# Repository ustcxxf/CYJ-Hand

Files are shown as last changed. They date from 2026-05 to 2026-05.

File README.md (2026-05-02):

# Customize-Your-Joy-hand (CYJ-Hand)

&emsp;&emsp;Humanoid dexterous hands have significant potential in pros-thetics, service robotics, and high-performance manipulation. However, existing designs often struggle to balance the chal-lenging requirements of lightweight design, high biomimicry, personalized customization, and low cost. To address these challenges, we present the CYJ Hand (Customize-Your-Joy Hand), an innovative 22-DOF humanoid dexterous hand. Fea-turing a highly biomimetic structure, the CYJ system weighs only 750 grams（forearm included）. Its modular design supports user-oriented customization while simplifying assembly, maintenance, and functional expansion. Inspired by Da Vinci’s mechanics, the CYJ Hand integrates a novel, controllable ten-don mechanism that allows for reconfigurable tendon routing and actuation system to meet diverse needs. Constructed with 3D printing and affordable commercial materials, the hardware cost for the CYJ Hand structure (excluding actuators) is under $60. Experimental results demonstrate that the CYJ Hand achieves a 100% success rate in both the Kapandji Test and GRASP taxonomy, and further exhibits dynamic grasping, in-hand manipulation, sub-millimeter motion repeatability (~0.7 mm), and reliable load-bearing performance, validating its exceptional dexterity and biomimetic design. With its com-prehensive advantages and innovations， the CYJ Hand pro-vides a versatile platform for the future applications and re-search in personalized prosthetics and dexterous robotic ma-nipulation, bridging the gap between high dexterity and acces-sibility in humanoid robotics. Related files and methods are open-sourced at GitHub repository.

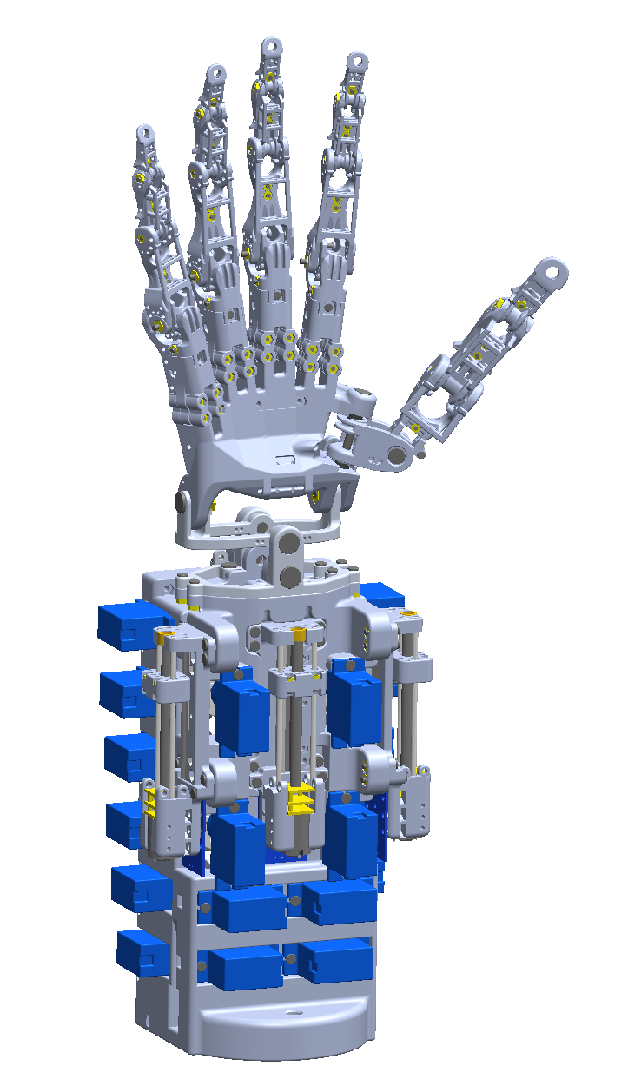
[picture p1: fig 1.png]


<center><font size=3><b>Figure 1 </b> CYJ Hand + Arm</font></center>

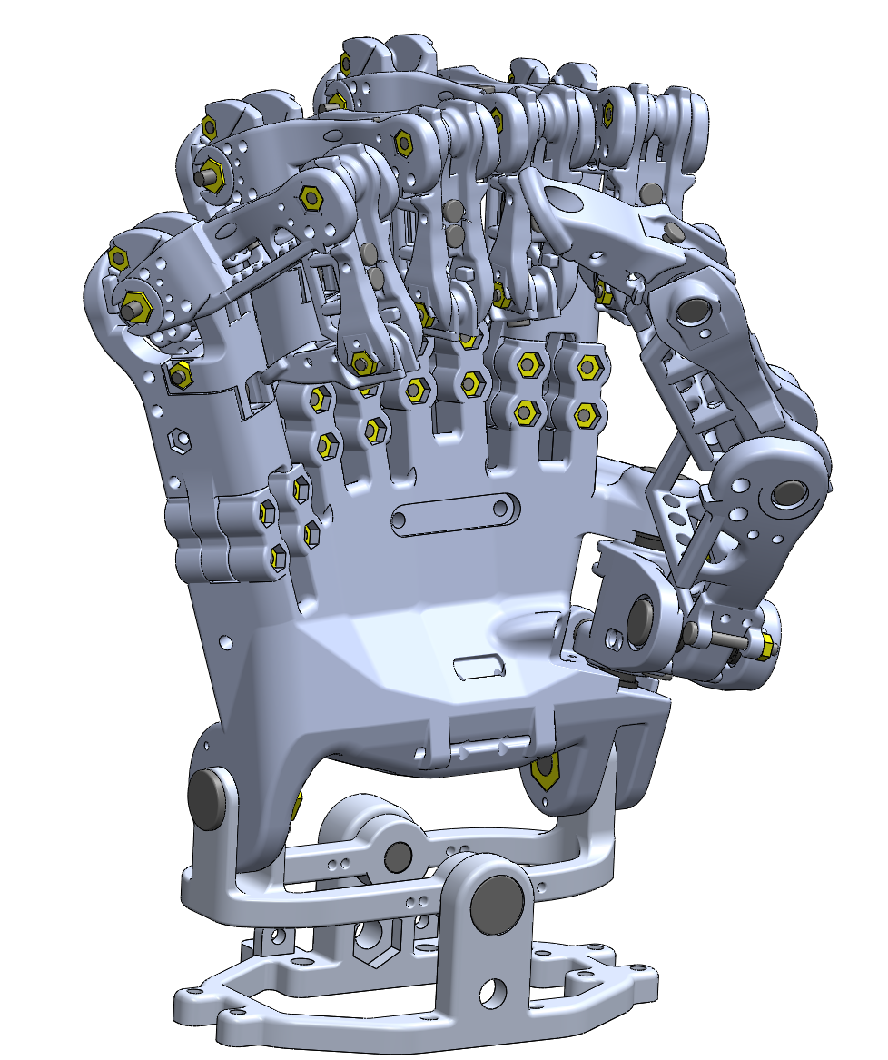
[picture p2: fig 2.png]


<center><font size=3><b>Figure 2 </b> CYJ Hand</font></center>

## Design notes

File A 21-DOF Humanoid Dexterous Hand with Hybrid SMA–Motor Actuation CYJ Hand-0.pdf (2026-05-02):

1

Abstract—CYJ Hand-0 is a 21-DOF humanoid dexterous hand featuring a hybrid tendon-driven actuation system that combines shape memory alloys (SMAs) and DC motors. The hand employs high-strength fishing line as artificial tendons and uses a fully 3D-printed AlSi10Mg metal frame designed to replicate the skeletal and tendon-muscle structure of the human hand. A linear motor-driven module controls finger flexion, while an SMA-based module enables finger extension and lateral abduction. These modules are integrated into a compact hybrid actuation unit mounted on a custom rear support structure. Mechanical and kinematic experiments, conducted under an Arduino Mega 2560-based control system, validate the effectiveness of the design and demonstrate its biomimetic dexterity.
Index Terms-- Humanoid dexterous hand, hybrid actuation, tendon-driven mechanism, 3D printing, biomimetic robotics
I. INTRODUCTION
From the late 20th century to the early 21st century, the concept of “robots” has transitioned from science fiction into tangible reality. Initially designed for simple, specialized tasks, robots have progressively undertaken increasingly complex, precise, and critical roles in industry and military. Among these, robotic manipulators stand as the earliest industrial robots and the foundation of modern robotics, liberating humans from laborious tasks and facilitating mechanization and automation. Moreover, they operate effectively in hazardous environments, thereby enhancing safety in sectors including machinery manufacturing, metallurgy, electronics, light industry, and nuclear energy.
The human hand represents the pinnacle of biological evolution, exhibiting extraordinary dexterity and versatility. Humanoid dexterous hands (HDHs) strive to replicate the intricate form, structure, and function of the human hand to enable similarly flexible and delicate manipulation. They hold immense promise for diverse applications spanning medical assistance, domestic services, intelligent manufacturing, space exploration, oceanic development, and public safety [1].
The history of prosthetic hands dates back to Roman times circa 200 B.C., where early wooden prostheses primarily served cosmetic or rudimentary functional purposes. The 19th century witnessed the invention of the tendon-driven, single-degree-of-freedom prosthetic hand by Peter Baliff, powered by the user’s limb movement—a fundamental principle that persists in contemporary prosthetics. The advent of the Belgrade hand [2] by Tomovic and Bonic in 1962

*Research supported by the National Science Foundation of China (Grant number: 61773358).
All authors are associated with the key Laboratory of Precision and Intelligent Chemistry, Institute of Humanoid Robots, Department of Precision Machinery and Precision Instrumentation, University of Science and Technology of China, Hefei, Anhui, 230026, PRC (*Corresponding author is Erbao Dong and can be contacted at e-mail: ebdong@ustc.edu.cn) marked a milestone, ushering in a new era of HDHs research. Since then, academic institutions and technology companies worldwide have pursued extensive research, yielding significant advancements such as the Okada hand [3], Stanford/JPL hand [4], Utah/MIT hand [5], and Robonaut hand [6]. With the advent of the 21st century, breakthroughs in sensor technology, human-computer interaction, bionics, and artificial intelligence have driven the evolution of HDHs towards greater diversity, miniaturization, and intelligence, exemplified by innovations like the Cyber hand[7], Tokyo hand [7] and UT hand [8].
Despite these advances, existing HDHs are often constrained by limited structural biomimicry, insufficient degrees of freedom (DOF), inadequate sensory capabilities, limited flexibility and coordination, low load-bearing capacity, fragile impact resistance, and high manufacturing costs. To address these challenges, the CYJ Hand-0 proposed herein incorporates the following key features:
- A highly biomimetic skeletal and joint structure with 21 DOFs (excluding the wrist).
- A flexible tendon-driven system utilizing high-strength fishing line.
- A hybrid actuation scheme integrating a shape memory alloy (SMA) linear drive module with double-amplified stroke and a DC brush motor linear drive module.
- Integration of the actuation system into a custom-designed robotic arm.
- Fabrication through cost-effective, easily manufacturable AlSi10Mg metal 3D printing, resulting in a total mass of only 380 grams.
- A fundamental control system based on the Arduino Mega2560 microcontroller for single-finger and full-hand operation.
- Single-finger load capacity of 1.2 kgf and an overall hand load capacity of 8 kgf.
- Capability to perform all Kapandji tests, 32 distinct gesture actions, and over 30 grasping experiments.
The remainder of this paper is structured as follows: The first section elaborates on the hand’s overall structural design, key components, kinematic modeling, and mechanical analysis of the flexible tendon drive. The second section details the SMA linear flexible drive module, DC brush motor linear drive module, system integration, and control framework. The last section presents performance evaluations in force, motion, dexterity, and grasping ability. Finally, the Conclusion summarizes the work and discusses future research directions.

II. MATERIALS AND METHODS
A. Bionic principle

## A 21-DOF Humanoid Dexterous Hand with Hybrid SMA-Motor Actuation: CYJ Hand-0 *

Jin Chai, Xiang Yao, Mengfan Hou, Yanghong Li and Erbao Dong*

2

The human hand’s main anatomical structures can be categorized into eight primary components: bones, tendons, ligaments, muscles, blood vessels, nerves, fatty tissue, and skin. The skeletal system is notably complex, comprising a total of 27 bones, which include 8 carpal bones, 5 metacarpal bones, and 14 phalanges [9]. The carpal bones are located within the wrist and are classified as radial or ulnar based on their anatomical position. The metacarpal bones articulate with the carpal bones at their bases via the carpometacarpal (CMC) joints, while the phalanges of each finger connect to the metacarpophalangeal (MCP) joints proximally. For the four fingers other than the thumb, each joint chain consists of the MCP joint, proximal interphalangeal (PIP) joint, and distal interphalangeal (DIP) joint, progressing from the proximal to the distal end. Due to mechanical constraints inherent to the interphalangeal joints, the MCP joint allows flexion and extension between 0° and 90°, and lateral deviation between –15° and 15°. The PIP joint exhibits a flexion range from 0° to 110°, while the DIP joint allows motion from 0° to 90° [10]. Furthermore, based on anatomical principles, the DIP joint flexes simultaneously with the PIP joint in the index, middle, ring, and little fingers, establishing a dynamic intra-finger coupling. This relationship is mathematically expressed in Eq.
(1) and illustrated in Fig. 1.
(1)

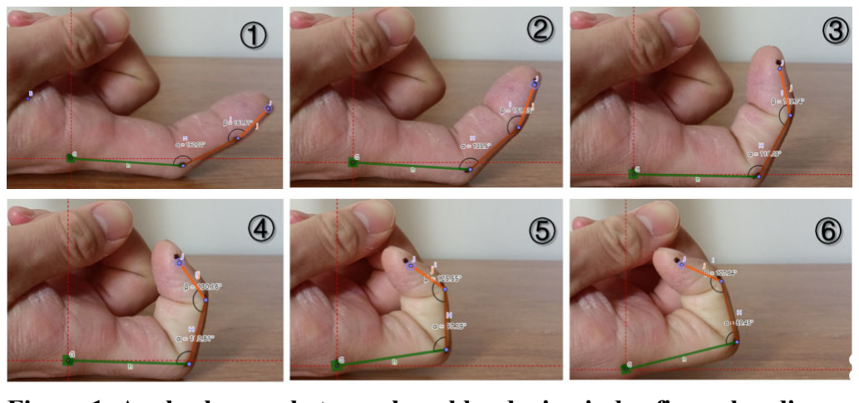
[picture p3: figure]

The structure of the thumb differs from that of the other four fingers in that it comprises only three joints: the carpometacarpal (CMC), metacarpophalangeal (MCP), and distal interphalangeal (DIP) joints, lacking a proximal interphalangeal joint. The thumb’s carpometacarpal joint, also known as the trapeziometacarpal (TMC) joint, grants it significantly greater mobility and strength compared to the other fingers. This joint facilitates a wide range of motions, including rotation (~17°), adduction and abduction (~42°), flexion and extension (~45°), as well as opposition—the ability to cross the palm. Consequently, the thumb exhibits exceptional dexterity. Traditionally, the TMC joint was considered to have 3-DOF [11], which, combined with the rest of the hand, results in a total of 21-DOF. However, subsequent research has revealed that the articular surfaces between the trapezium and the first metacarpal are saddle-shaped, with the axes for adduction-abduction (Ab-Ad) and flexion-extension (Fl-Ex) being neither orthogonal nor intersecting [12]. Most contemporary biomimetic hands, such as the Etho hand, implement the thumb’s TMC joint as a 2-DOF ball joint. While ball-and-socket joints provide smooth movement that approximates 2-DOF, their structural configuration differs from that of the human thumb and typically requires up to three actuators and six tendons for control.
The DOFs of the human hand are commonly simplified to

### 20 by omitting subtle motions, including active or passive

rotation of each finger around its longitudinal axis [13] (as illustrated in Fig. 2a), the complex kinematics of the thumb’s

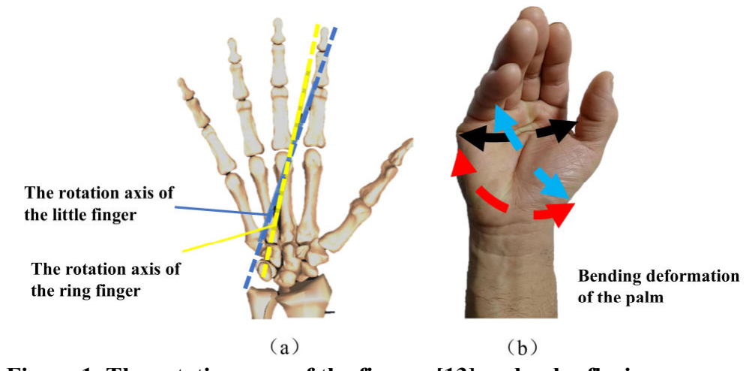
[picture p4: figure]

TMC joint, flexion and deformation of the palm (Fig. 2b), and the DOFs of the wrist.
B. Overall structure and 3D prototype
The overall structural design of the CYJ Hand-0 is illustrated in Fig. 3a. All components are named according to their anatomical counterparts in the human hand, including the thumb, index finger, middle finger, ring finger, little finger, metacarpals, carpals, and wrist. Notably, the thumb's metacarpal structure is divided into two distinct segments: the medial adduction carpometacarpal joint and the rotational carpometacarpal joint, which will be described in detail later. In addition, the index, middle, and ring fingers adopt a unified structural design to simplify fabrication and enhance component interchangeability.
As shown in Fig. 3b, the CYJ Hand-0 consists of 18 distinct component types, totaling 80 individual parts. To improve modularity and reduce manufacturing costs, many joints share identical components. The hand is not only anatomically inspired in appearance but also replicates the skeletal structure of a human hand at a 1:1 scale in both form and assembly, as depicted in Fig. 3c. The total mass of the hand is 380 g, which accounts for less than 0.575% of the body weight of an average 75 kg adult male (approximately 413 g for a human hand). As shown in Fig. 3d, the unique mechanical design of the bionic hand enables up to 21 DOFs, excluding the wrist.
C. Structural design of key components
The index finger structure of the CYJ Hand-0 serves as a universal design, also applied to the middle and ring fingers. Each universal finger consists of 9 distinct component types—including the proximal, middle, and distal phalanges—resulting in a total of 12 individual parts. To ensure optimal functional performance and structural integrity, the design incorporates sliding bearings and adopts a biomimetic shape that closely replicates the interphalangeal joints of the human finger. The structural layout and dimensions of the universal finger are shown in Fig. 4. The little finger differs from this universal structure only in the length of the proximal phalanx and a few minor structural details, as illustrated in Fig. 5a.

Figure 1. Angle changes between knuckles during index finger bending.

Figure 1. The rotation axes of the fingers [13] and palm flexion.

3

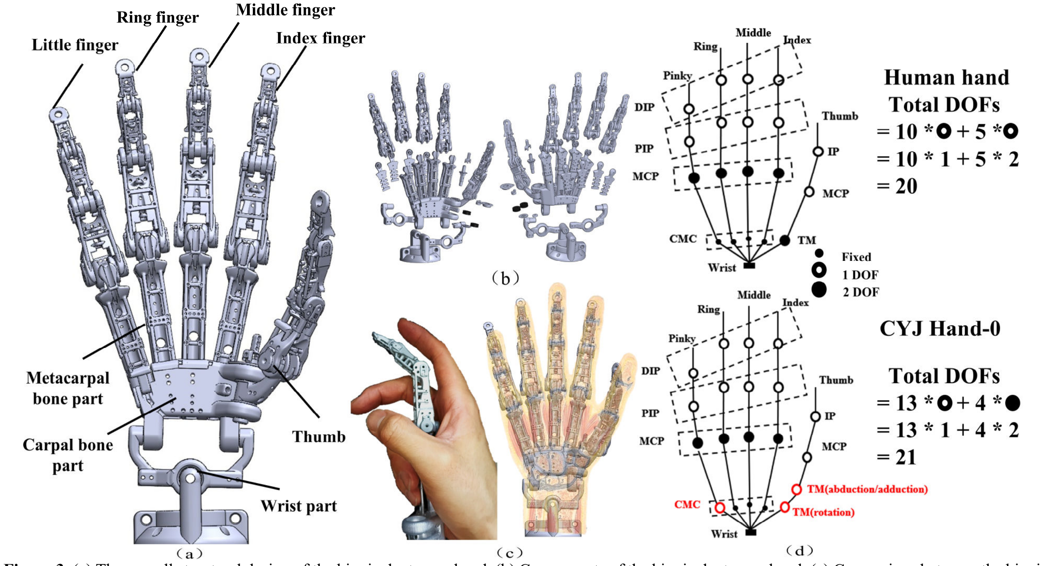
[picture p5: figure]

The thumb, being the most flexible and complex digit of the CYJ Hand-0, adopts a customized structural design. To balance structural simplicity with functional fidelity, the thumb’s metacarpal is divided into two segments at the carpometacarpal (CMC) joint: one responsible for adduction/abduction and the other for flexion/extension. The adduction/abduction module is structurally similar to the metacarpophalangeal (MCP) joints of the other fingers. This design choice reduces the overall degrees of freedom, enhances joint modularity, and simplifies mechanical implementation, as shown in Fig. 5b.
The joint rotation ranges of the CYJ Hand-0 are designed to match those of the human hand and are compared with representative existing bionic hands in Table I.
TABLE I. | COMPARISONS OF THE HDHS
Hand | Weight (g) | Interphalangeal joint rotation angle | Thumb joint rotation angle
MCP (°) | PIP (°) | DIP (°) | Ab-Ad (°) | Ex-Fl (°)
Human hand | 431 | 0-90 | 0-110 | 0-90 | 0-70 | 0-70
CYJ Hand-0 | 380 | 0-90 | 0-110 | 0-90 | 0-53 | 0-107
Robotic hand | | 0-90 | 0-110 | 0-90 | 0-90 | 0-90
Tact hand | 350 | 0-90 | 23-90 | 0-20 | 0-90 | 0-105
Dextrus hand | 428 | 0-90 | 0-90 | 0-90 | 0-90 | 0-120
Bebionic hand | 550 | 0-90 | 0-90 | 0-20 | | 0-68
i-Limb hand | 600 | 0-90 | 0-90 | 0-20 | 0-60 | 0-95
The metacarpal bones of the human hand are numerous, tightly packed, and arranged in a complex three-dimensional configuration. To enhance the anatomical fidelity of the palmar structure in the CYJ Hand-0—while minimizing unnecessary internal space and reducing weight—an interchangeable metacarpal design and an integrated carpal bone structure were developed, as illustrated in Fig. 5c. Notably, the metacarpal bones of the four fingers and the base connecting to the carpal region are not arranged in a parallel manner. Instead, they are positioned at specific angles relative to one another, forming a naturally concave geometry

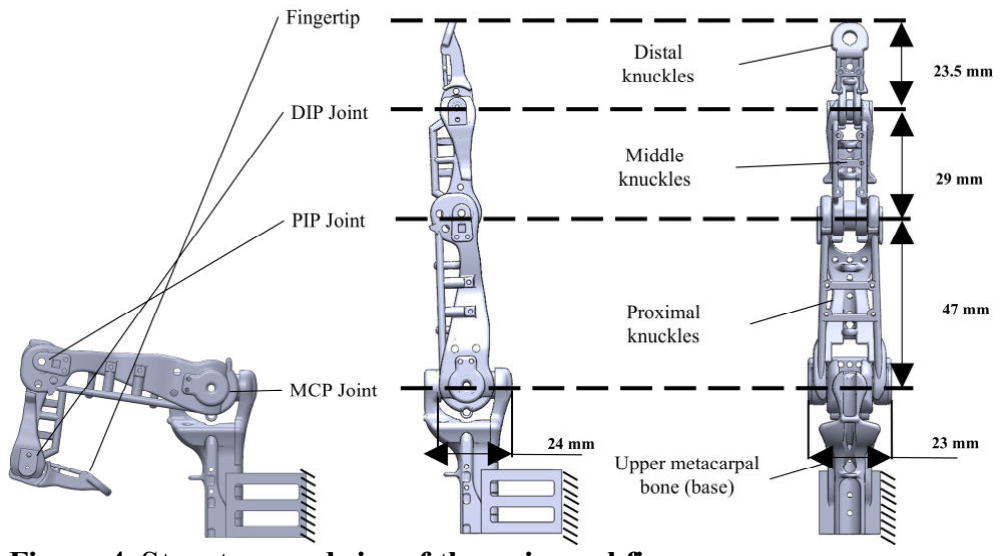
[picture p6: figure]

that mimics the human palm. This curvature enables the CYJ Hand-0 to achieve a cupped palm configuration, thereby enhancing its grasping performance, as shown in Fig. 5d.
D. Kinematic modeling of the fingers
Each finger of the CYJ Hand-0 can be thought of as a small, open-chain, rotationally articulated, tandem robot. The entire hand is equivalent to multiple such robots connected in parallel. The universal finger mechanism belongs to the side-swinging type 4-joint finger structure, as shown in Fig. 6a. The axes of joints 1 and 2 at the metacarpophalangeal joint are orthogonal to each other. Joints 3 and 4 represent the proximal and distal phalanges respectively. The axes of joints 2, 3 and 4 are always parallel. the finger linkage coordinate system is established according to the D-H theory, as shown in Fig. 6b.
Define | as the fixed reference coordinate system 0.
Define the origin as the point where the axes of joints 1 and 2 intersect. X and Y form the right-handed system. The lengths

Figure 3. (a) The overall structural design of the bionic dexterous hand. (b) Components of the bionic dexterous hand. (c) Comparison between the bionic dexterous hand and human hand. (d) Comparison of DOFs between the bionic dexterous hand and human hand.

Figure 4. Structure and size of the universal finger.

4

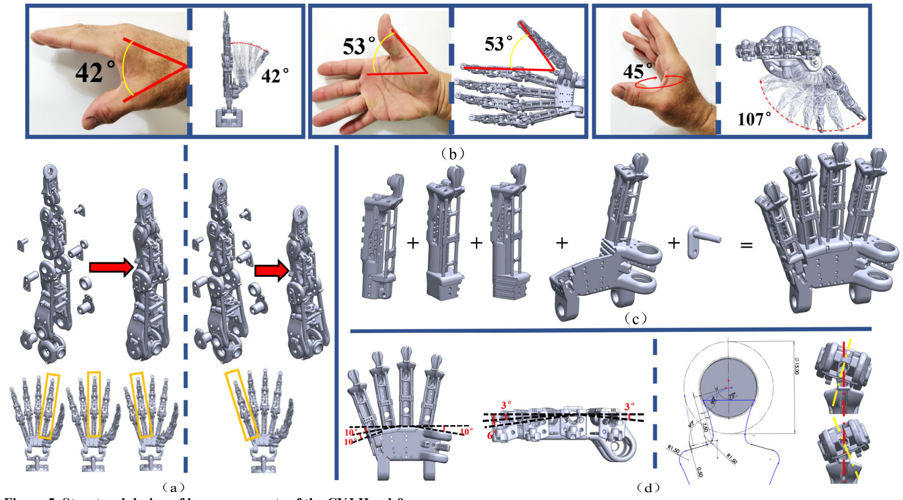
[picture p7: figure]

of the phalanges are , , and . The angles of rotation of
the joints are | , | , | and | . The axes of the lateral
pendulum joints at the metacarpophalangeal joints are perpendicular to the axes of the flexion joints at
angles | . The coordinates of the position of the finger
tip in the fixed reference system are | . See Table Ⅱ
below for detailed D-H parameters.

TABLE II. D-H PARAMETERS FOR THE UNIVERSAL FINGERS

1 0 | 0 | 0 | -15~15
2 90 | 47 | 0 | 0~90
3 0 | 29 | 0 | 0~110
4 0 | 23.5 | 0 | 0~90
The following paragraph discusses the solution to forward kinematics for a finger. The homogeneous transformation matrix that describes the position and orientation of the coordinate system at the fingertip relative to the fixed
Therefore, with known values of , | , | and | , the
position coordinates | of the general fingertip can be

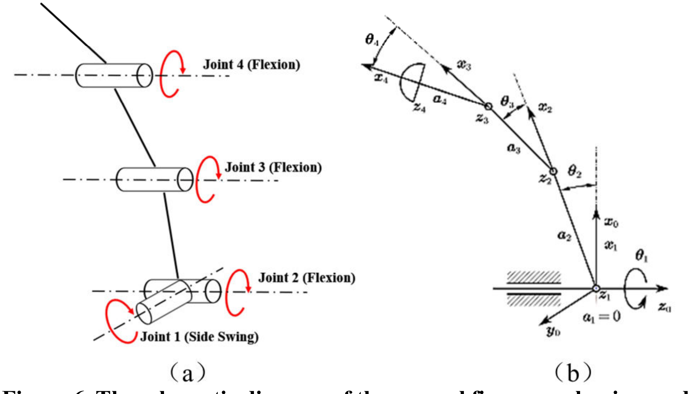
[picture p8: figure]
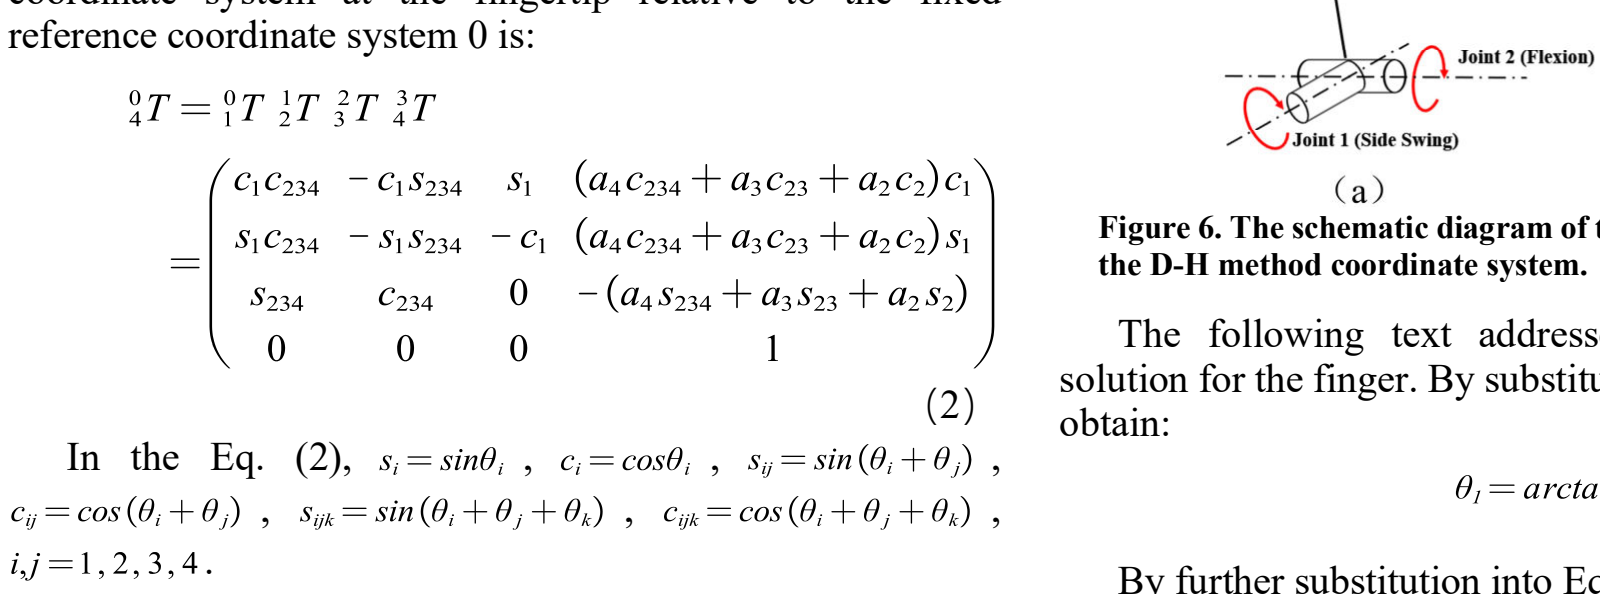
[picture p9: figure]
reference coordinate system 0 is:; In the Eq. (2),; obtain:; the D-H method coordinate system.

The following text addresses the inverse kinematics solution for the finger. By substituting into Eq. (3) and (4), we

(6)

By further substitution into Eq. (1), we obtain:
（7）

Figure 6. The schematic diagram of the general finger mechanism and

Figure 5. Structural design of key components of the CYJ Hand-0.

5

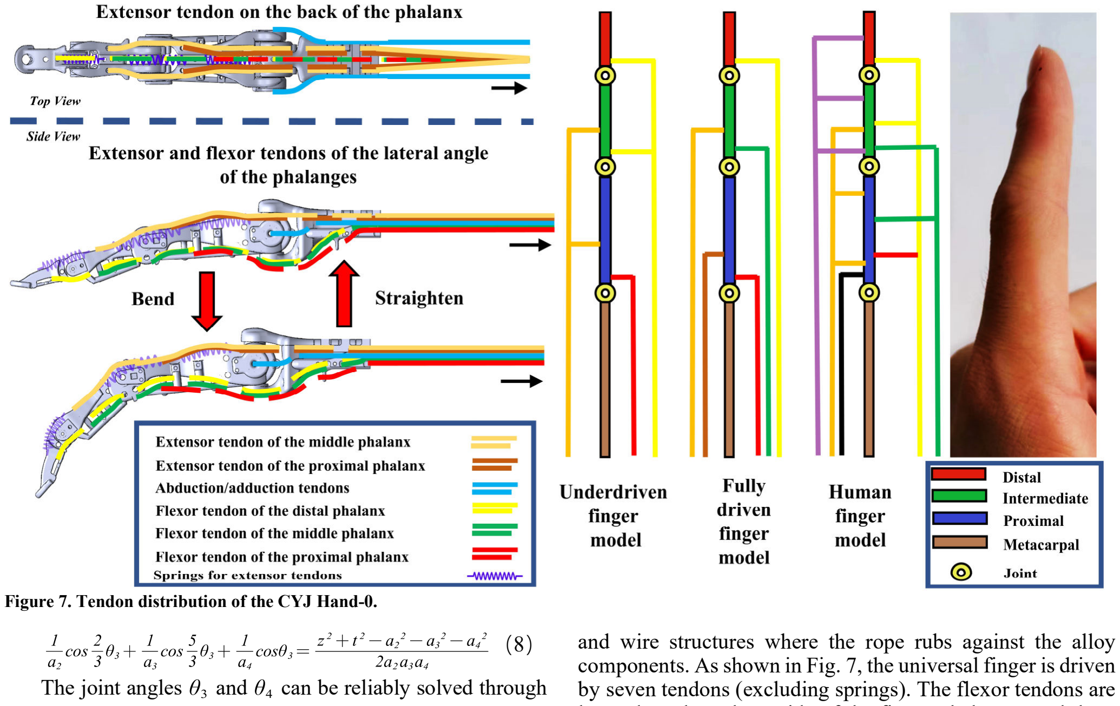
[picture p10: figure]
The joint angles; and; can be reliably solved through

numerical methods, and then substituted back into Eq. (3) to solve for using Newton's iteration method. Thus, with the known position coordinates of the fingertip ((x, y, z)), the joint
angles , , | and | can be determined.
E. Numerical simulation for finger tendon
The CYJ Hand-0 utilizes high-powered fishing line as a tendon. These tendons are fixed at one end to the phalanges and connected to linear actuators at the other, transmitting force and torque over a distance. Such tendons possess high strength, light weight, and an ability to absorb impacts that gear transmissions lack. Here we use a 12-braid high-powered fishing line with a mark of 9.0, a diameter of 0.55mm and a nominal maximum pull of 40kg. At the distal end of the tendons, the rope is commonly secured using the figure-eight loop method and the double fisherman's knot technique.

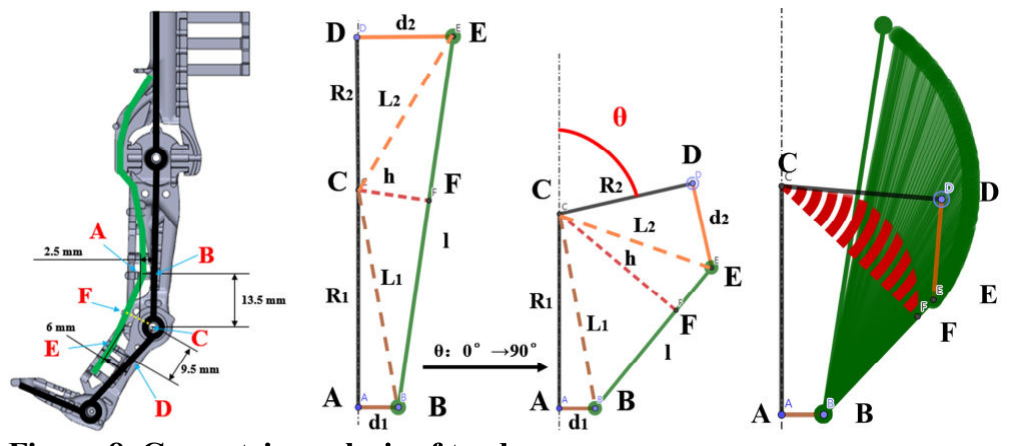
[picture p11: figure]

The tendons have a fixed path of travel at each finger joint. Grease is used to reduce friction at the edges of holes, tubes and wire structures where the rope rubs against the alloy components. As shown in Fig. 7, the universal finger is driven by seven tendons (excluding springs). The flexor tendons are located on the palmar side of the finger phalanges and there are three of them that drive the proximal, middle and distal phalanges in flexion. The extensor tendons, located on the dorsal side of the finger phalanges, are two in number and drive the proximal and middle phalanges to extend back to their original positions. The distal phalanx is not driven by an additional tendon and is reset by a pre-tensioned spring. The two abduction/adduction lateral tendons, located on both sides of the finger, with one side stretching while the other relaxes when the finger swings.
The metacarpophalangeal joint, proximal and distal knuckles have the same configuration. Among them, the proximal phalangeal joint has a high load-bearing capacity and is more frequently used in the human hand. We take it as the object of analysis in GeoGebra, and the analysis is shown

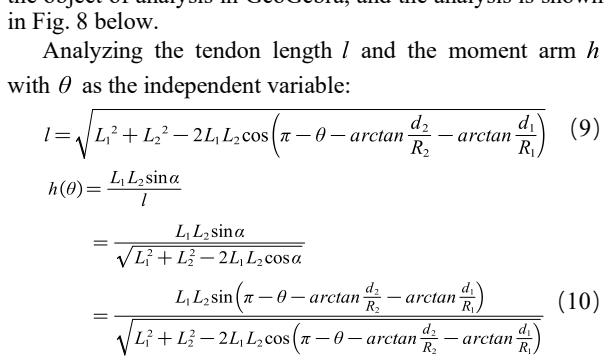
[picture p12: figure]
in Fig. 8 below.; with as the independent variable:

Analyzing the tendon length and the moment arm

Substitute the data of the proximal joint of the universal finger to plot and analyze. As shown in Fig. 9a, the red line represents the tendon length at the joint and the black line represents the fitted straight line. The tendon length gradually

Figure 7. Tendon distribution of the CYJ Hand-0.

Figure 8. Geometric analysis of tendons.

6

shortens by 16.86 mm over the course of the joint angle from 0° to 110°. It means that at least 20 mm of work needed to be done at the driver end of the straight line. This means that the linear actuator needs to perform work at least a 20mm distance. As shown in Fig. 9b, the red line represents the force arm of the tendon and the black line represents the fitted straight line, which increases over the course of the joint angle from 0° to 90°. The increase in the force arm reduces the stretching force on the tendon, making it easier for the finger to perform the

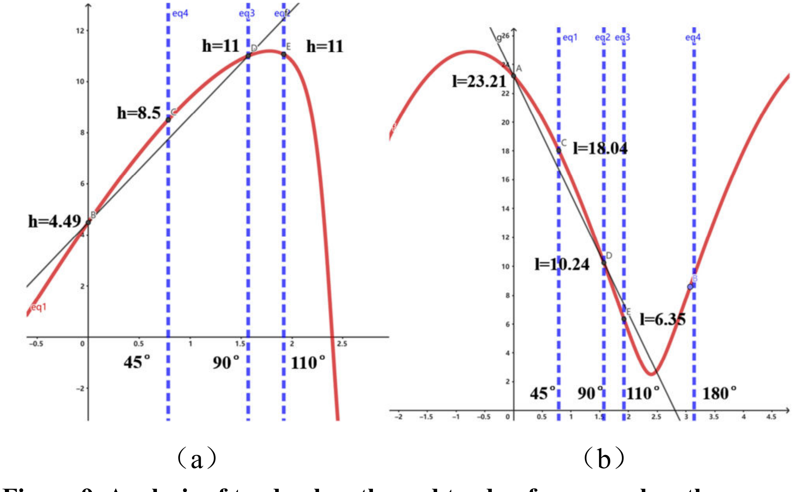
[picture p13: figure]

bending maneuver under load and to output a greater force/moment at the end of the finger.
III. DESIGN AND CONSTRUCTION OF THE DRIVE SYSTEM
The integrated solution of the driven system of the CYJ Hand-0 is an important innovation of the overall design. Unlike traditional motor or pneumatic/hydraulic drives, the bionic dexterity hand introduces not only a DC brush motor drive module system to drive the finger flexion, but also an SMA linear drive module system to drive the finger side-swing and straightening movements. They form the SMA-motor hybrid driven module system together.
A. Abbreviations and Acronyms
The SMA driven module uses Ni-Ti alloy wires of DYNALLOY from US (detailed parameters as shown in Table Ⅲ). The SMA material has a shape memory effect, which is a deformability and workability resulting from the martensite-austenite phase change that occurs between low and high temperatures of the material. The method of controlling the module is energized heating. The maximum displacement output is 18 mm and the maximum output force is 784 N. The module construction is shown in Fig. 10.

TABLE III. PARAMETERS OF SMA WIRE
Parameters | Value
Density | 6.45g/cm³
Phase transition temperature | 90°C
Specific heat capacity | 837J/(kg·K)
Thermal conductivity | 18W/(m·K)
Poisson's ratio | 0.33
Coefficient of martensitic thermal expansion | 6.6×10⁻⁶ /°C
Coefficient of austenitic thermal expansion | 11.0×10⁻⁶ /°C
B. Motor driven module
Finger flexion is driven by a screw nut motor (GA12-N20-298, parameters shown in Table IV) drive module. The module drives the tendons to rotate the phalanges relative to the joints so that the fingers are flexed. A single motor driven module has dimensions of 73.25mm in height, 33mm in length, and 25mm in width, with a working stroke of 20mm, a self-weight of 40g, and a rated output force of 400N. The models of the motor and the motor driven module are shown in Fig. 11.

TABLE IV. PARAMETERS OF SMA WIRE
Parameters | Value
Rated voltage | 12 V
Rated current | 0.18 A
Rated speed | 100 RPM

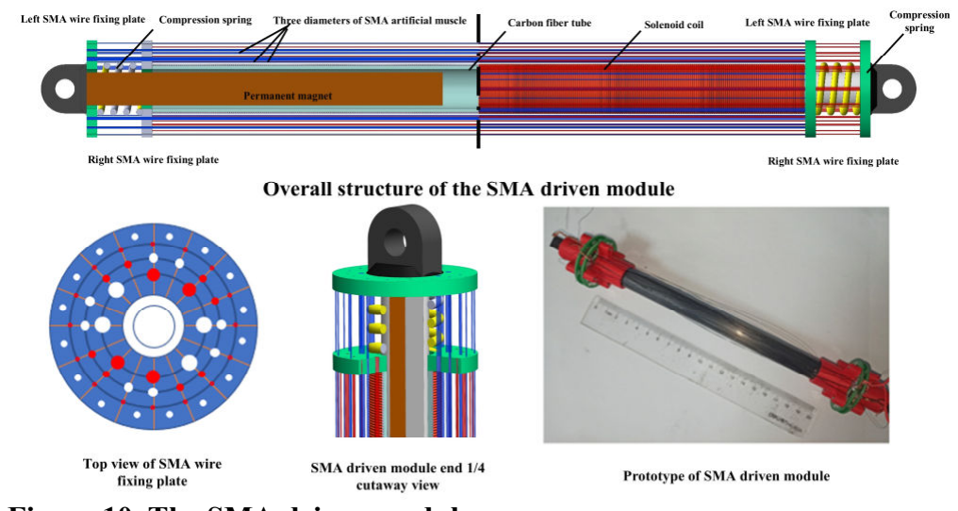
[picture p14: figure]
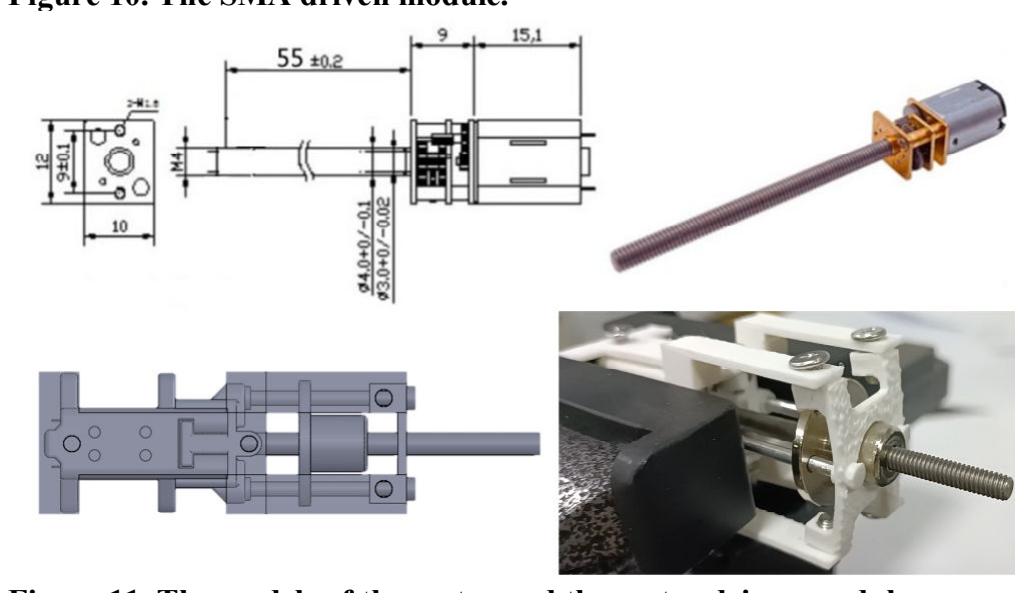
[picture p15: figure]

Rated torque | 1.5 kg·cm
Pitch of screw | 0.7 mm
C. The integrated SMA-motor hybrid driven system
In the SMA driven module, SMA wires of larger diameter have a lower response frequency and higher output force. SMA wires of smaller diameter have a higher response frequency and lower output force. Besides, the electromagnetic coil and permanent magnet in the SMA driven module can make up for the shortcomings of the SMA wires. They can form a linear driven module with adjustable size of output force, frequency and fast response speed. The
Figure 9. Analysis of tendon lengths and tendon force arm lengths. | Figure 10. The SMA driven module.

Figure 11. The models of the motor and the motor driven module

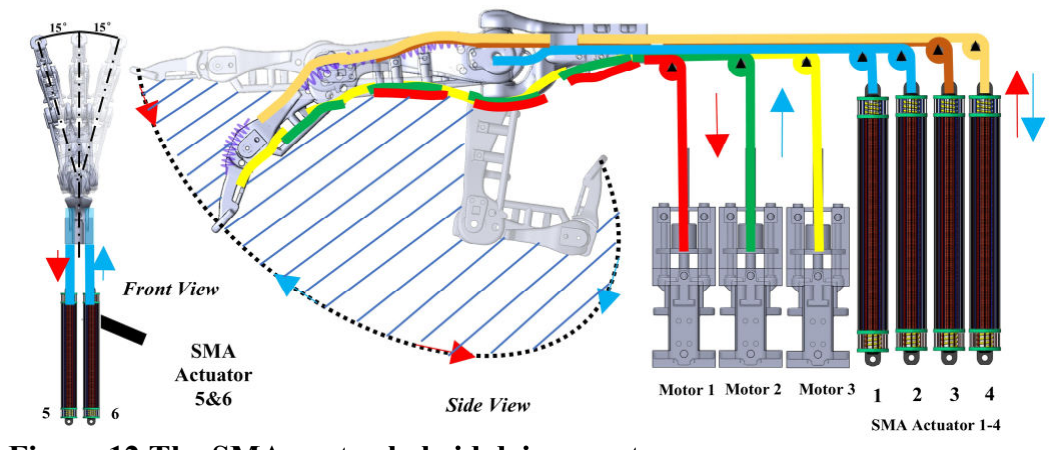
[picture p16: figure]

Figure 12 The SMA-motor hybrid driven system.

7

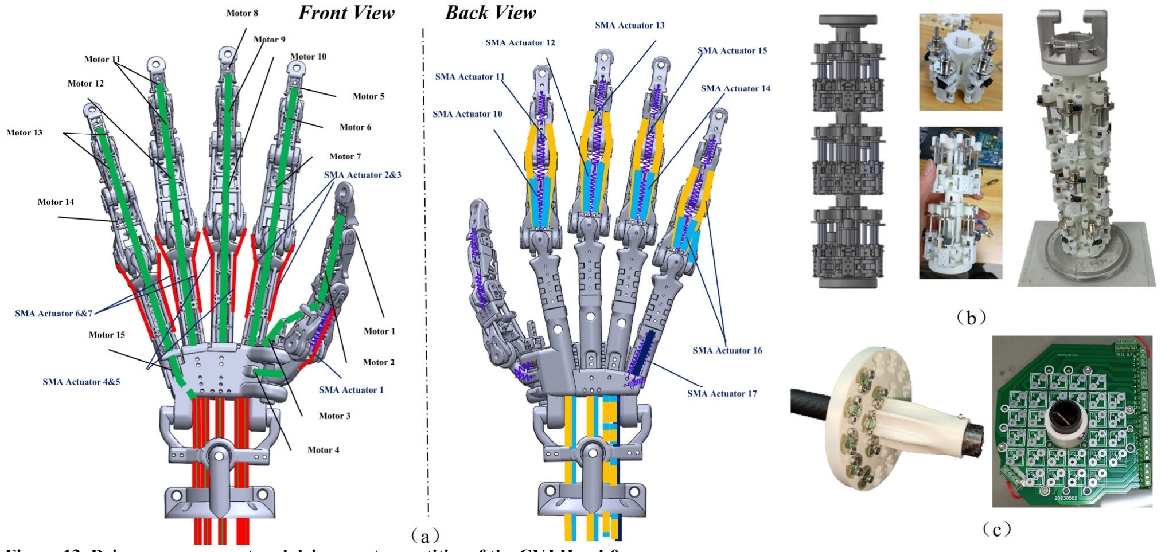
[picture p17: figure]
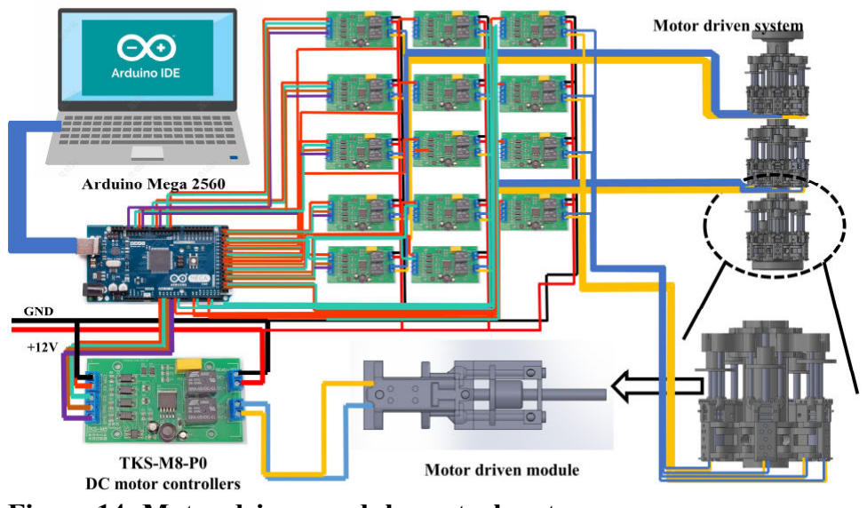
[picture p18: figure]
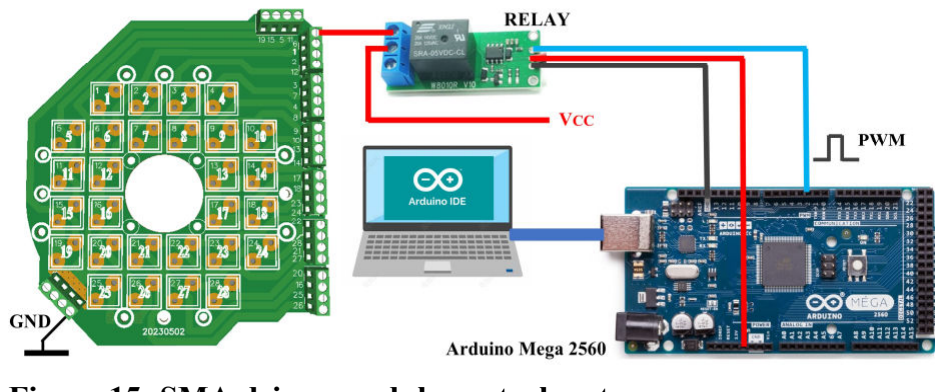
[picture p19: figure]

motor driven module features a small but stable output force, self-locking capability, high output displacement accuracy and slow speed (1.17mm/s). As a result, the hybrid driven system constructed by combining the two driven modules has the particularly comprehensive advantages of adjustable response frequency, high output force range and high output displacement accuracy.
As shown in Fig. 12, the motor driven module drives the finger flexion. With the help of the spring, the SMA linear actuator module drives the finger to straighten or to swing sideways. When the finger is flexed, the motor turns the screw forcibly, causing the nut to drop and the flexor tendon to be stretched. At this time, the SMA linear drive module maintains its original length and the extensor tendon relaxes. As the finger is straightened, the motor drives the screw to reverse the rotation of the nut, causing the flexor tendon to relax. At this point the SMA driven module is energized and heated and the extensor tendon is tensed. The SMA wires and the spring on the back of the phalanx together drive the phalanx to extend until it returns to its original position. After the finger is returned to its original position, the SMA driven module is switched off to dissipate heat and the extensor tendons are relaxed as the SMA wires are restored to their original length. The CYJ Hand-0 has a total of 21 DOFs. The total number of actuators (TNA) is 32, with a total of 17 SMA driven

Figure 13. Driven arrangement and driven system entities of the CYJ Hand-0.

Figure 14. Motor driven module control system.

Figure 15. SMA driven module control system.

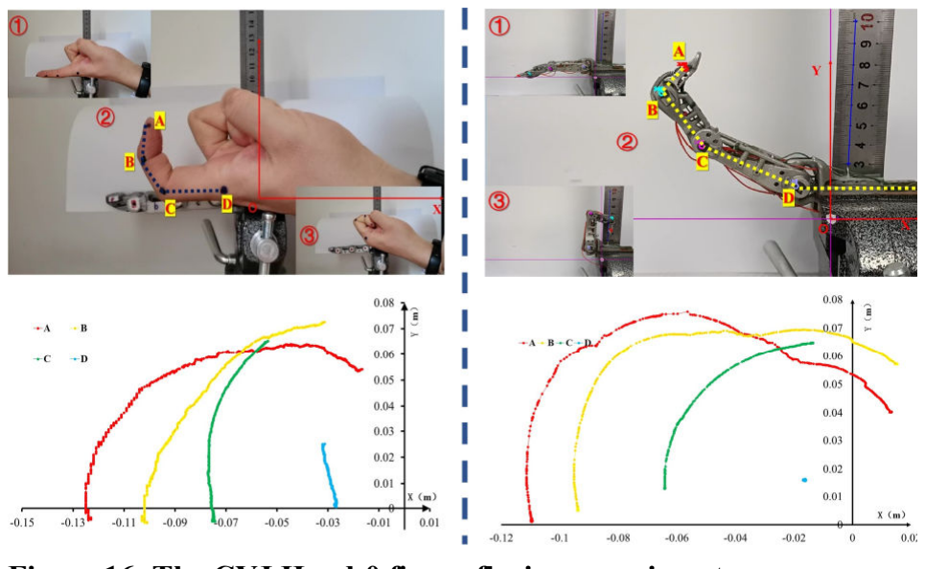
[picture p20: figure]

Figure 16. The CYJ Hand-0 finger flexion experiment.

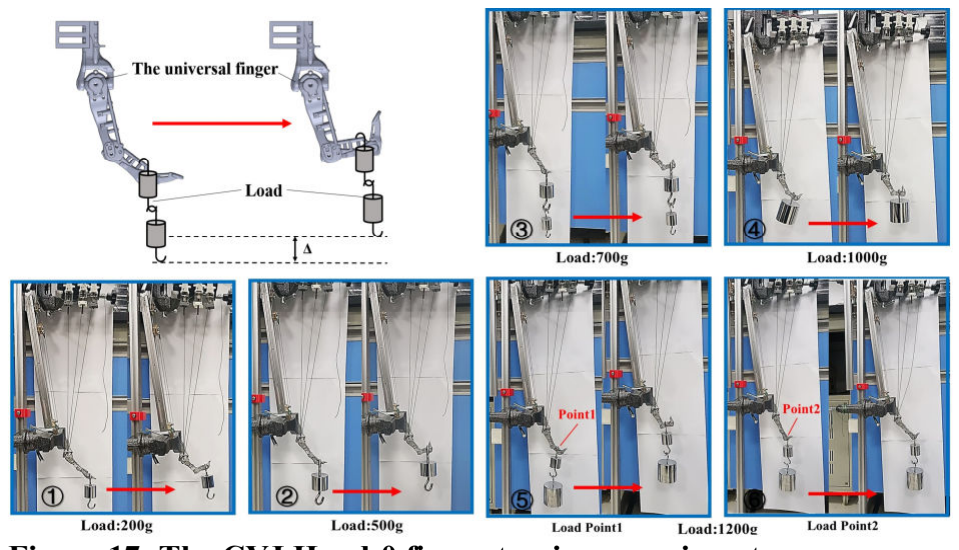
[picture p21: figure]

Figure 17. The CYJ Hand-0 finger tension experiments.

8

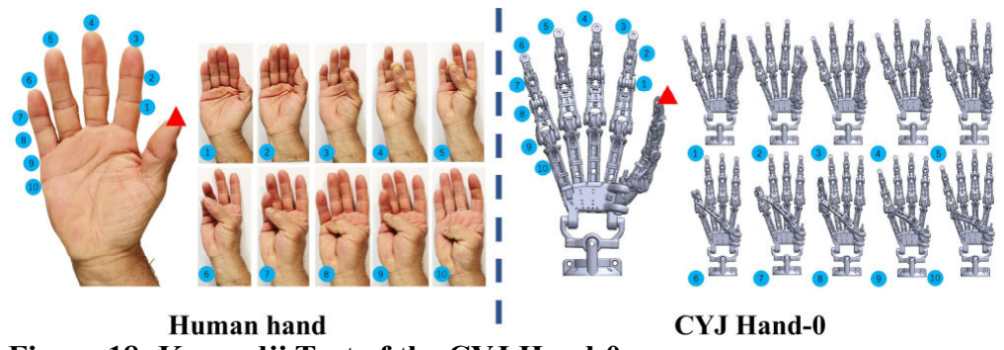
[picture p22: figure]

modules and 15 motor driven modules. The overall driven arrangement is shown in Fig. 13a. In the figure, the motor refers to the end position of the tendon driven by the motor driven module and the SMA actuator refers to the end position of the tendon driven by the SMA driven module.
Numerous external SMA driven modules and motor driven modules must be integrated into the arm attached to the end of the wrist of the bionic dexterous hand to facilitate the transmission of force and displacement through tendons. As shown in Fig.13b, a robotic arm is constructed by arranging 15 motor driven modules in a configuration of five motor driven modules circularly arranged on one layer, stacked over three layers. The robotic arm is 3D printed in white resin with a total weight of 780 g. Its upper part is connected to the wrist of the bionic dexterous hand, and the lower part is matched with the end of UR10. Its hollow structure is used to transfer the tendons. A gap is left between every two motor driven modules to arrange an SMA driven module. 12 SMA driven modules are integrated as shown in Fig. 13c.
D. Control system
The CYJ Hand-0 is equipped with an electrical motor driven module control system, which is based on the Arduino Mega2560 and 15 Tonkeys TKS-M8-P0 DC motor controllers, as shown in Fig 14. The computer controls the corresponding motor controllers by sending commands to the microcontroller, enabling controllable forward/reverse rotation and start/stop functionality for the different motors.
For the SMA driven module system, a PWM-relay control system as shown in Figure 15 is used—the relays controlling the power supply on/off for each SMA driven module are managed by the high and low level PWM signals output from the Arduino microcontroller.

IV. EXPERIMENTS
Based on the aforementioned modeling and theoretical analysis, the following sections evaluate the structural feasibility, actuation performance, and overall biomimicry and dexterity of the CYJ Hand-0 through a series of experiments.
A. Finger experiments
In the CYJ Hand-0 finger flexion experiment, the video processing software Tracker is used for image analysis. Tracker analyses each frame to obtain the time-position information of each joint node, so as to obtain the value of the joint angle at different moments and perform subsequent processing, as shown in Figure 16.
In the finger tension experiments of the CYJ Hand-0, the distal phalanx was selected as the output point for tension measurement, consistent with human usage habits. The load applied to the universal finger was gradually increased from 200 g to 1200 g, and all tests were successfully completed, as shown in Fig. 17. Although the fingertip pulling force did not reach the maximum level of human fingers, the structural load-bearing capacity of a single finger exceeded 4 kg. Notably, during the pulling tests exceeding 1.5 kg, the motor experienced overload and burned out. A single-finger load of 1.2 kg implies that the entire CYJ Hand-0 can support a total load of approximately 8 kg.
B. Gesture experiments
The first experiment was a CYJ Hand-0 gesture simulation.

Figure 18. Kapandji Test of the CYJ Hand-0.

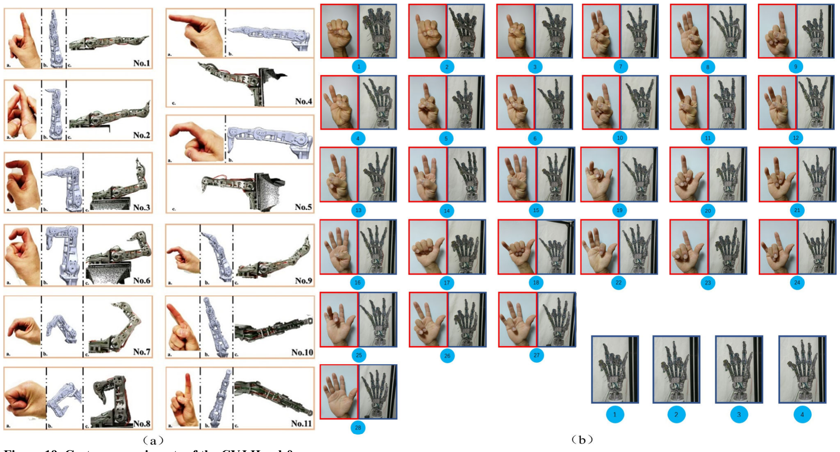
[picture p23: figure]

Figure 19. Gesture experiments of the CYJ Hand-0.

9

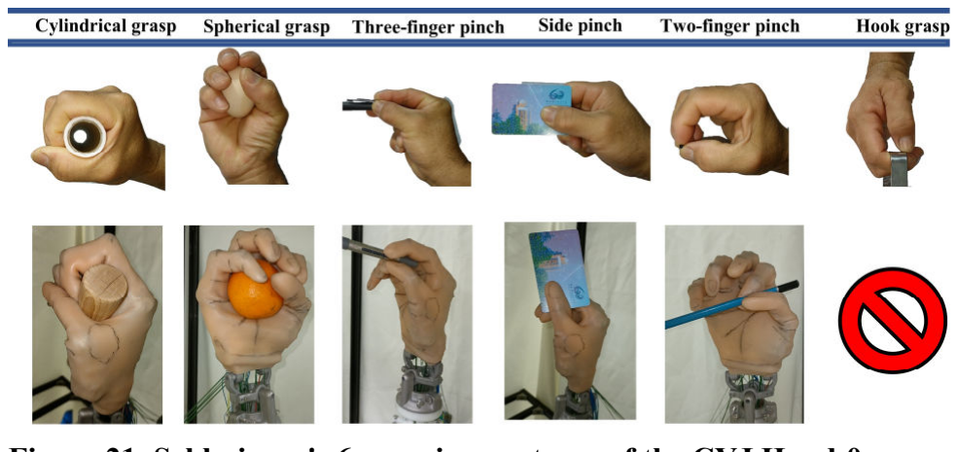
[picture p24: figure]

Referring to the test proposed by Ibrahim A. Kapandji in 1985 for measuring the dexterity of the thumb and palm of the human hand (Kapandji Test [14]), whether the tip of the thumb is able to touch the typical part of the hand is taken as the assessment index. As shown in Fig. 18, thanks to its unique structural design, the bionic dexterous hand can perform the same 10 combinations of movements as the human hand.
To further demonstrate the bionic and dexterity of the CYJ Hand-0. In the finger gesture comparison experiment between human hand and the CYJ Hand-0, shown in Fig. 19a, we used

### 11 gestures commonly used by the index finger, which is more

flexible in the human hand. According to the relationship between the movements of the five fingers, there are 28 gestures that the human hand can generally perform without external force, and 4 gestures that are difficult to perform without external force. In the gesture comparison experiment between the human hand and the CYJ Hand-0, as shown in Fig. 19b, the CYJ Hand-0 successfully performed all 32 gestures.
C. Grasping experiments
The biggest difference between the human hand and other mechanical grips is its flexibility and versatility. Thanks to the good use of the human hand to develop and use various tools suitable for the human hand, we have embarked on the path of transforming and conquering nature. In order to reflect the function of the CYJ Hand-0, a series of grasping experiments on various objects are carried out below.
According to Schlesinger [15], human hand grasping postures can be divided into six types based on different object shapes and the position used by the human hand: cylindrical grasp, spherical grasp, three-finger pinch, side pinch, two-finger pinch, and hook grasp. Fig. 21 demonstrates five of these postures achieved by the CYJ Hand-0 (the hook grasp was not tested).
Further, the grasping modes of the human hand were categorized into 16 more specific ones according to Cutkosky's classification method [16], as shown in Fig. 22a. The CYJ Hand-0 completes 9 of these postures in the experiment, as shown in Fig. 22b.
In addition to grasping experiments based on traditional classification methods, as shown in Figs. 20 and 21, we also attempted gesture experiments such as grasping a pen (Fig. 22a) and grasping a full-filled water bottle (Fig. 22b), in which the full-filled water bottle was a 550 ml mineral water bottle. It is further verified that the CYJ Hand-0 has the ability to grasp a certain load.
V. CONCLUSION
In this study, we proposed a high-DOF dexterous hand based on a hybrid SMA–motor drive. This paper describes the overall structural design of the CYJ Hand-0, including key components such as the thumb and metacarpal bone. The hand features 21-DOF, a highly biomimetic and flexible

Figure 20. The CYJ Hand-0 with flesh and skin.

Figure 21. Schlesinger's 6 grasping postures of the CYJ Hand-0.

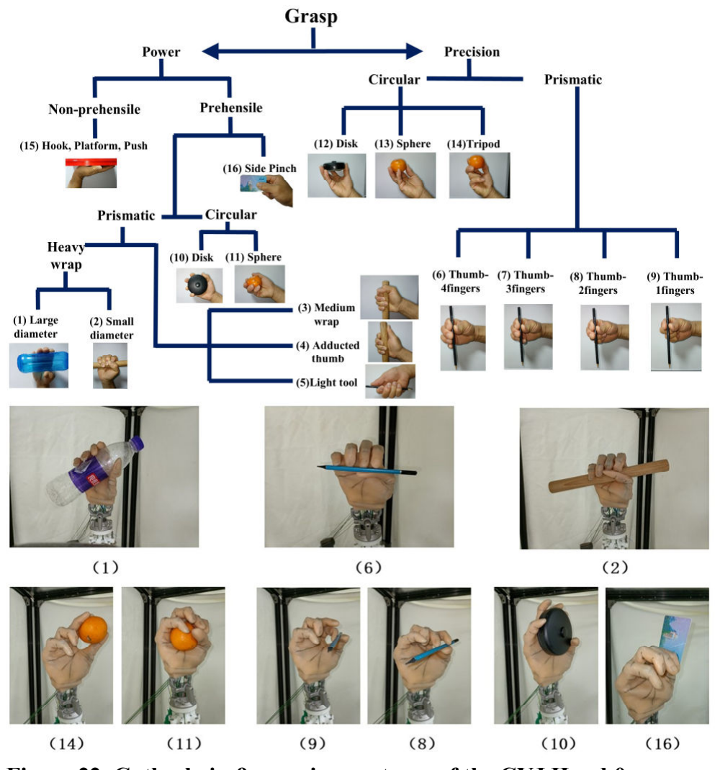
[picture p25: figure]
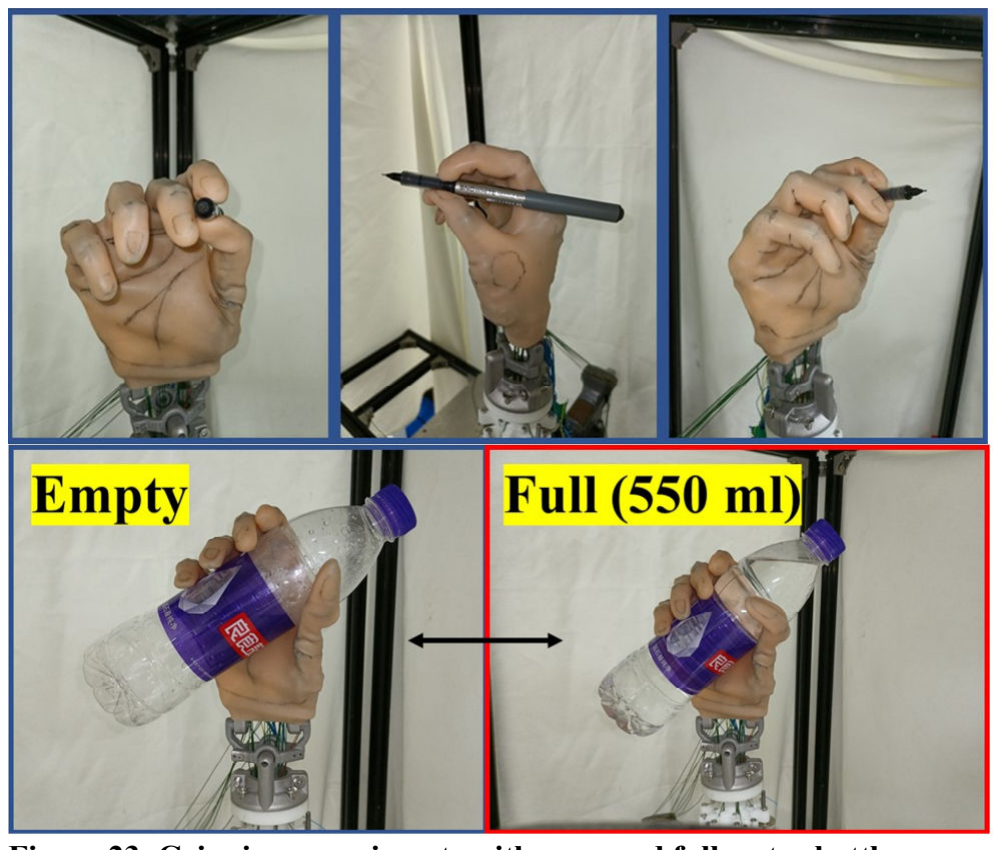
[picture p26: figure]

Figure 22. Cutkosky's 9 grasping postures of the CYJ Hand-0. | Figure 23. Gripping experiments with pens and full water bottles.

10

structure, and all parts are fabricated using metal 3D printing technology.
This paper also presents the design of the hybrid drive system. The SMA–motor hybrid actuation module we proposed is a key innovation. Comprising motor drive modules and SMA drive modules, the hybrid system offers unique and comprehensive advantages, such as adjustable response frequency, a wide output force range, and high output displacement accuracy. Additionally, we proposed a robotic arm integrated with both motor and SMA drive modules, which is externally mounted at the end of the CYJ Hand-0 to serve as both the power source and support structure. Finally, we developed a basic drive control system based on the Arduino Mega2560 microcontroller.
In future work, we plan to optimize the structural design and actuation scheme of the CYJ Hand-0 based on experimental feedback. We will also improve the sensor system and closed-loop control system to further enhance the application value of the hand.

REFERENCES

[1] O. M. Andrychowicz et al., “Learning dexterous in-hand manipulation,” The International Journal of Robotics Research, vol. 39, no. 1, Art. no. 1, Jan. 2020.
[2] R. Tomovic and G. Boni, “An adaptive artificial hand,” IRE Trans. Autom. Control, vol. 7, no. 3, pp. 3–10, 1962.
[3] T. Okada, “Computer Control of Multijointed Finger System for Precise Object-Handling,” IEEE Trans. Syst., Man, Cybern., vol. 12, no. 3, Art. no. 3, 1982.
[4] C. Loucks, V. Johnson, P. Boissiere, G. Starr, and J. Steele, “Modeling and control of the stanford/JPL hand,” in Proceedings. 1987 IEEE International Conference on Robotics and Automation, Raleigh, NC, USA: Institute of Electrical and Electronics Engineers, 1987, pp. 573–578.
[5] S. C. Jacobsen, J. E. Wood, D. F. Knutti, and K. B. Biggers, “The UTAH/M.I.T. Dextrous Hand: Work in Progress,” The International Journal of Robotics Research, vol. 3, no. 4, Art. no. 4, Dec. 1984.
[6] C. S. Lovchik and M. A. Diftler, “The robonaut hand: a dexterous robot hand for space,” in Proceedings 1999 IEEE International Conference on Robotics and Automation (cat. No.99ch36288c), 1999, pp. 907–912 vol.2.
[7] M. C. Carrozza, G. Cappiello, S. Micera, B. B. Edin, L. Beccai, and C. Cipriani, “Design of a cybernetic hand for perception and action,” Biol. Cybern., vol. 95, no. 6, pp. 629–644, 2006.
[8] Bart et al., “UT hand I: a lock-based underactuated hand prosthesis,” Mech. Mach. Theory, 2014.
[9] H. Gray, H. Gray, and W. H. Lewis, “Anatomy of the Human Body.,” Postgraduate Medical Journal, vol. 42, no. 493, Art. no. 493, 1966.
[10] John Lin, Ying Wu, and T. S. Huang, “Modeling the constraints of human hand motion,” in Proceedings Workshop on Human Motion, Los Alamitos, CA, USA: IEEE Comput. Soc, 2000, pp. 121–126.
[11] L. Y. Chang and N. S. Pollard, “Method for Determining Kinematic Parameters of the In Vivo Thumb Carpometacarpal Joint,” IEEE Trans. Biomed. Eng., vol. 55, no. 7, Art. no. 7, Jul. 2008.
[12] J. J. Crisco, E. Halilaj, D. C. Moore, T. Patel, A.-P. C. Weiss, and A. L. Ladd, “In Vivo Kinematics of the Trapeziometacarpal Joint During Thumb Extension-Flexion and Abduction-Adduction,” The Journal of Hand Surgery, vol. 40, no. 2, Art. no. 2, Feb. 2015.
[13] J. H. Buffi, J. J. Crisco, and W. M. Murray, “A method for defining carpometacarpal joint kinematics from three-dimensional rotations of the metacarpal bones captured in vivo using computed tomography,” Journal of Biomechanics, vol. 46, no. 12, Art. no. 12, Aug. 2013.
[14] A. I. Kapandji, “Clinical test of apposition and counter-apposition of the thumb,” Annales de chirurgie de la main : organe officiel des societes de chirurgie de la main, vol. 5 1, pp. 67–73, 1986.
[15] G. Schlesinger, “Der mechanische Aufbau der künstlichen Glieder,” in Ersatzglieder und Arbeitshilfen: Für Kriegsbeschädigte und Unfallverletzte, M. Borchardt, K. Hartmann, Leymann, R. Radike, Schlesinger, and Schwiening, Eds., Berlin, Heidelberg: Springer, 1919, pp. 321–661.
[16] M. R. Cutkosky, “On grasp choice, grasp models, and the design of hands for manufacturing tasks,” IEEE Trans. Robot. Automat., vol. 5, no. 3, Art. no. 3, Jun. 1989.

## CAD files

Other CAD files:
Assembly of the CYJ Hand in STL file format/STL-format assembly of CYJ Hand.STL
1.10.5.STEP
STL/Arm/1.10.5 DrivenBackFix.STL
STL/Hand/Fingers/1.10.5 IndexFinger_Proximal Phalanx.STL
STL/Hand/Palm/1.10.5 Palm.STL
STL/Hand/Thumb/1.10.5 Thumb_Distal Phalanx.STL
STL/Hand/Waist/1.10.5 Waist_BackForward.STL
STL/LinearActuator/MotorActuator_ShiftingNut_Part1.STL
STL/Servo/SG92R_ArmBase_Modify.STL
STL/Arm/1.10.5 DrivenArm.STL
STL/Hand/Fingers/1.10.5 IndexFinger_Middle Phalanx.STL
STL/Hand/Thumb/1.10.5 Thumb_Proximal Phalanx 2.STL
STL/Hand/Waist/1.10.5 Waist__LeftRight.STL
STL/LinearActuator/MotorActuator_Column_80.STL
STL/Servo/SG92R_Base.STL
STL/Hand/Fingers/1.10.5 LittleFinger_Proximal Phalanx.STL
STL/Hand/Thumb/1.10.5 Thumb_Proximal Phalanx.STL
STL/LinearActuator/LinearSensor_47mm_Shift.STL
STL/Hand/Fingers/1.10.5 IndexFinger_Distal Phalanx.STL
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
